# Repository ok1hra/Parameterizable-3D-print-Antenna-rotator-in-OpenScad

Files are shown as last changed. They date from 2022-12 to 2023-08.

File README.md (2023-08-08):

# Parameterizable 3D print Antenna rotator in OpenScad
- Four predefined sizes (S,MS,M,XL)
- Included terminal for install motor from cordless drill
- Without nuts (tapered holes)
- DXF export lasered steel cover
- BOM included
- With Azimuth potentiometer (MS,M,XL)
- With Homing endstop, for using with stepper motor (MS,M,XL)

## Assembly manual
- [RemoteQTH Wiki](https://remoteqth.com/w/doku.php?id=3d-print-rotator)
- [GitHub copy](Assembly-manual.md)

## Related components
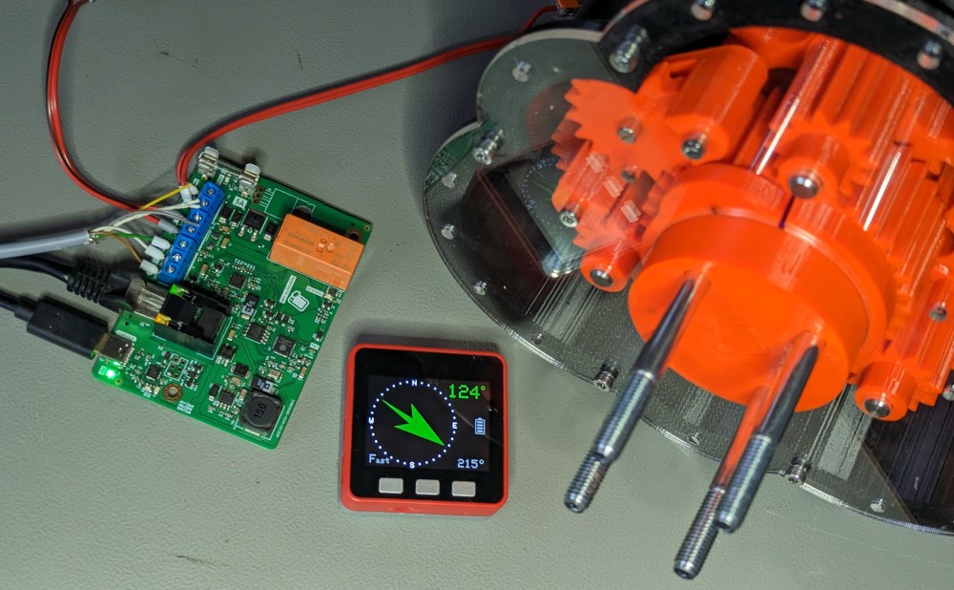
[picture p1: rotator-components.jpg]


- [IP-rotator firmware](https://github.com/ok1hra/IP-rotator)
- IP-rotator hardware - TBD
- [Gyrotator](https://github.com/ok1hra/gyrotator)

## Output files
- Source [OpenScad file](parametric-3d-rotator.scad) for design customisation
- Render bash script [.sh](render-stl.sh) need modify local path

### S size
(compromise design without endstop and azimuth potentiometer)
- [BOM](S.echo)
- Steel cover [.DXF](S.DXF)
- Steel output terminal [.DXF](Sout.DXF)
- All [.STL](/S)
- [S_in.3mf](S_in.3mf)
- [S_out.3mf](S_out.3mf)

### M size (recommended)
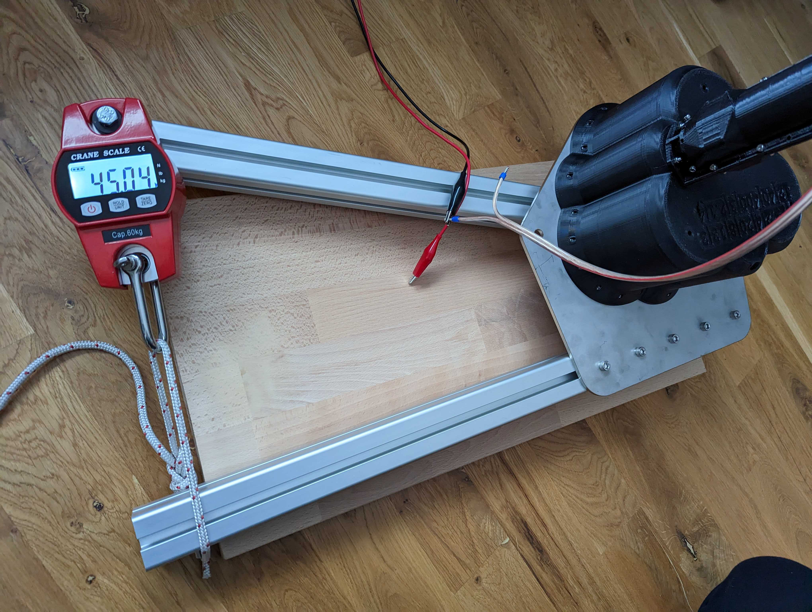
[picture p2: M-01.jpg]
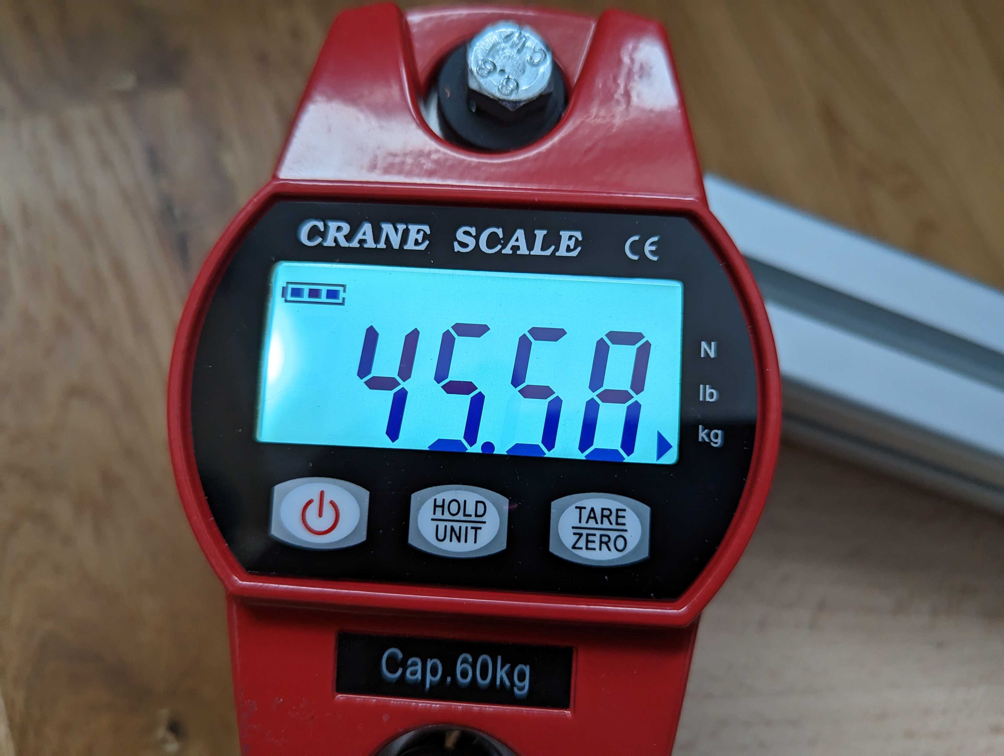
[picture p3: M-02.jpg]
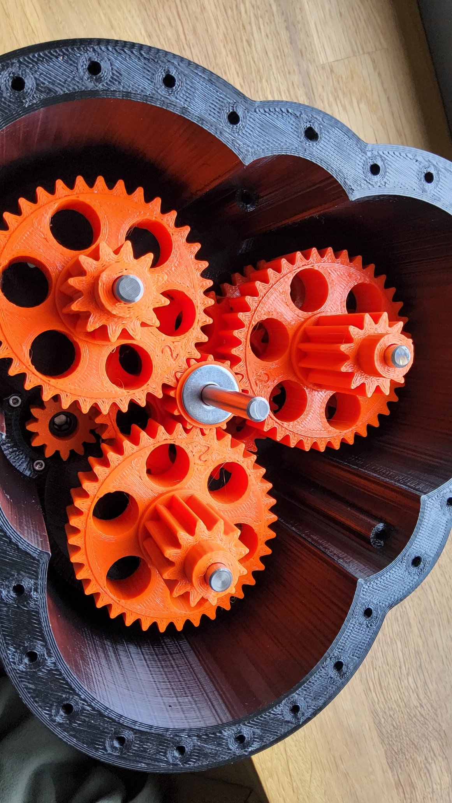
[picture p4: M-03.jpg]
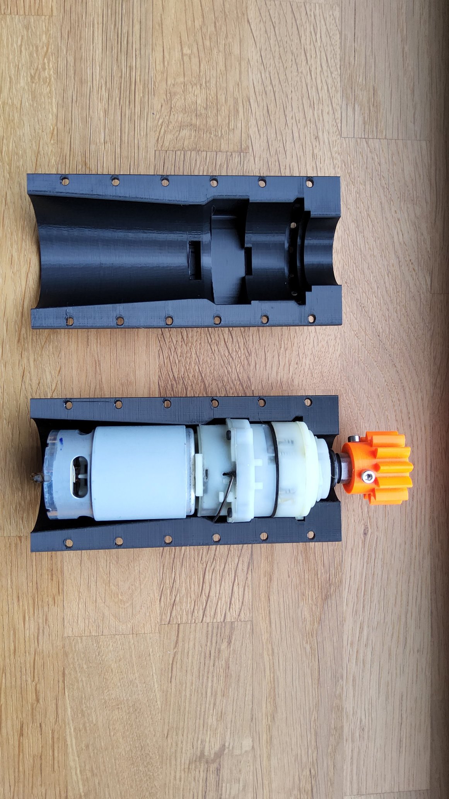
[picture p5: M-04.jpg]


- Max torque **2200 kg/cm (215 N/m)**
- [Torque video](https://www.youtube.com/watch?v=XpkWt55Bdf4)
- [BOM](M.echo)
- Steel cover [.DXF](M.DXF)
- Steel output terminal [.DXF](Mout.DXF)
- All [.STL](/M)
- [M_in.3mf](M_in.3mf)
- [M_out.3mf](M_out.3mf)

### MS size (smaller version for Prusa MK3 MK4 printers)
- [BOM](MS.echo)
- Steel cover [.DXF](MS.DXF)
- Steel output terminal [.DXF](MSout.DXF)
- All [.STL](/MS)
- [M_in.3mf](MS_in.3mf)

### XL size
- [BOM](XL.echo)
- Steel cover [.DXF](XL.DXF)
- Steel output terminal [.DXF](XLout.DXF)
- All [.STL](/XL)
- [XL_in.3mf](XL_in.3mf)
- [XL_out1.3mf](XL_out1.3mf)
- [XL_out2.3mf](XL_out2.3mf)

* [Homepage](https://remoteqth.com/3d-rotator.php)

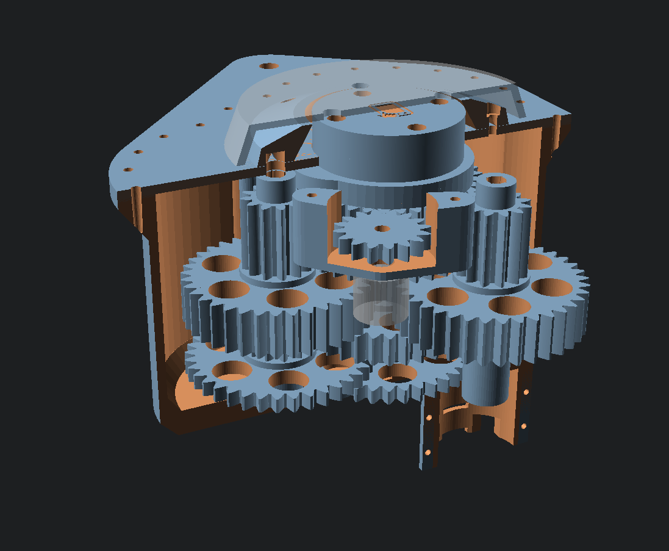
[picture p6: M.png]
preview

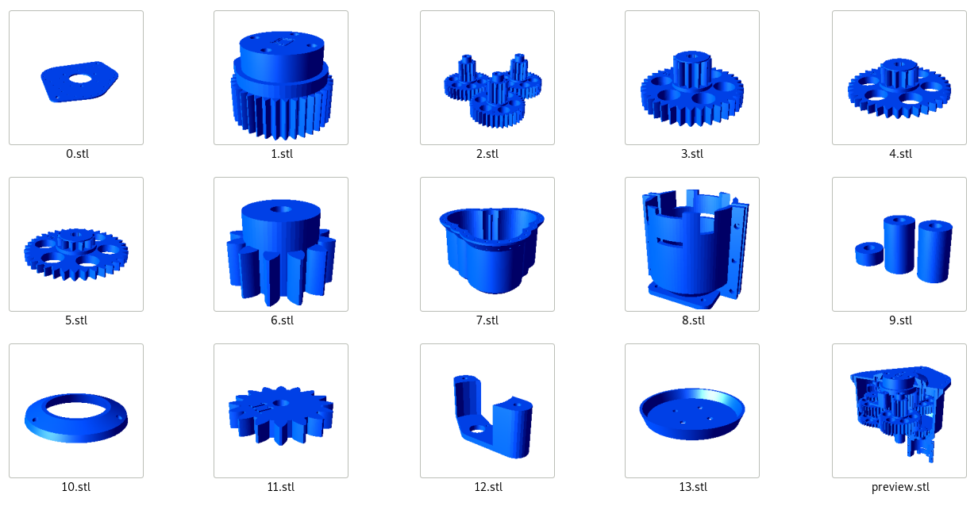
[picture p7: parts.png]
parts


* [OpenScad](https://openscad.org/)

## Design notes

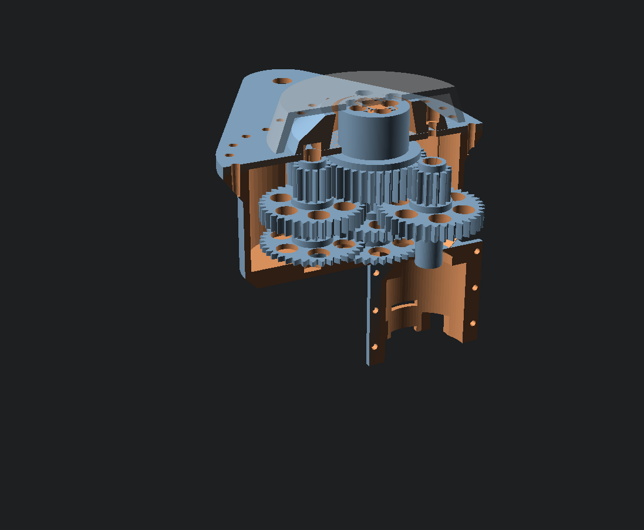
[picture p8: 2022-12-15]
S.png

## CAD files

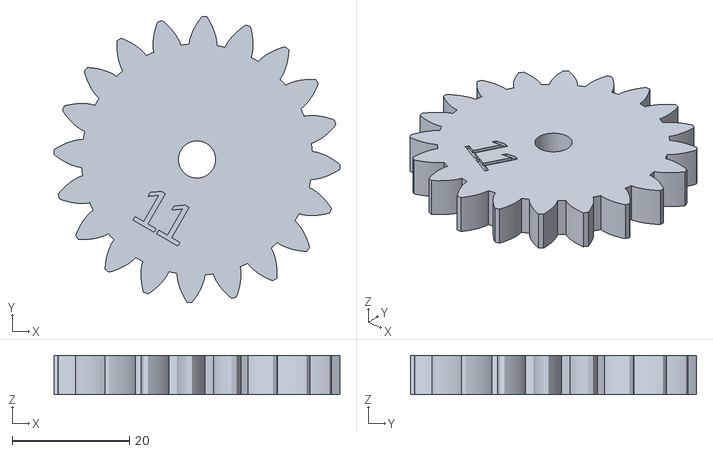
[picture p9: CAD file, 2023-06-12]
M/11.stl
48.9 x 48.9 x 6.67

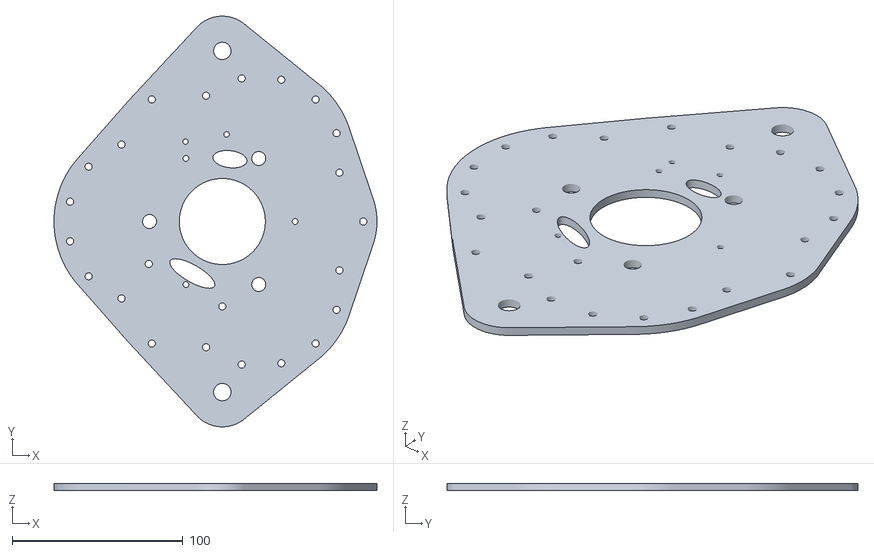
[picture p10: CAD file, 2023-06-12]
MS/0.stl
189.3 x 240.8 x 4.00

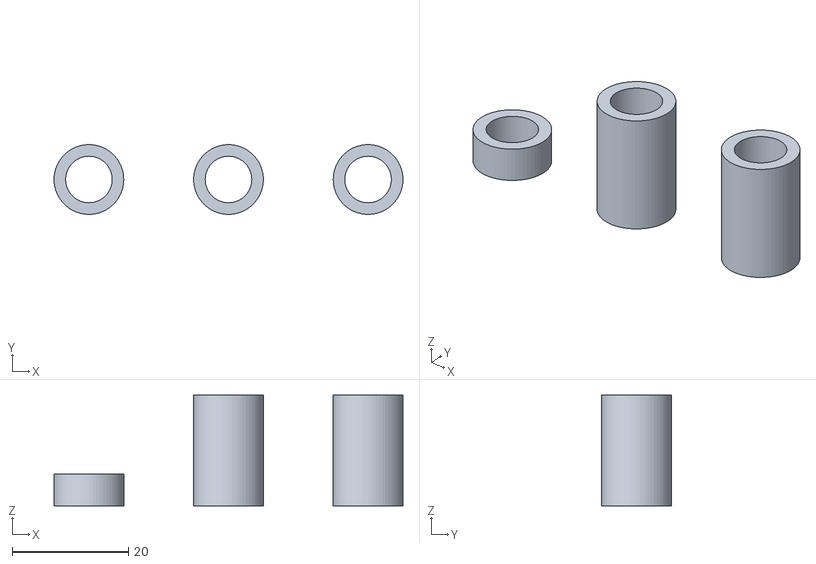
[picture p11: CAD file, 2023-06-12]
S/9.stl
60.0 x 12.0 x 19.0

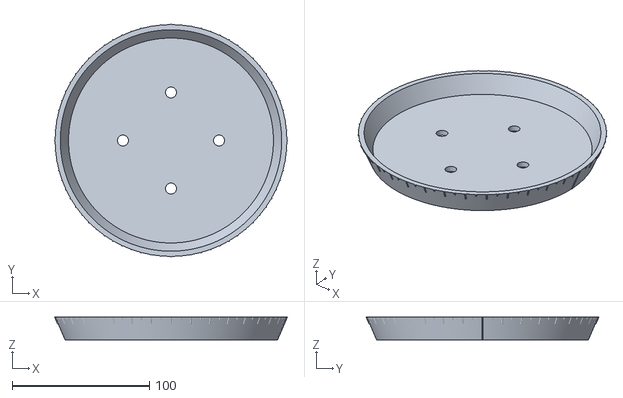
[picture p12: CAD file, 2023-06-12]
XL/13.stl
169.8 x 169.8 x 16.8

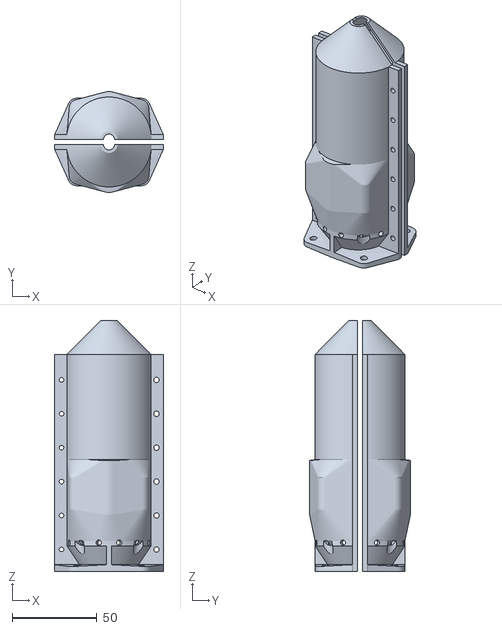
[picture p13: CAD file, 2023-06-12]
M/8.stl
64.0 x 59.5 x 148.0

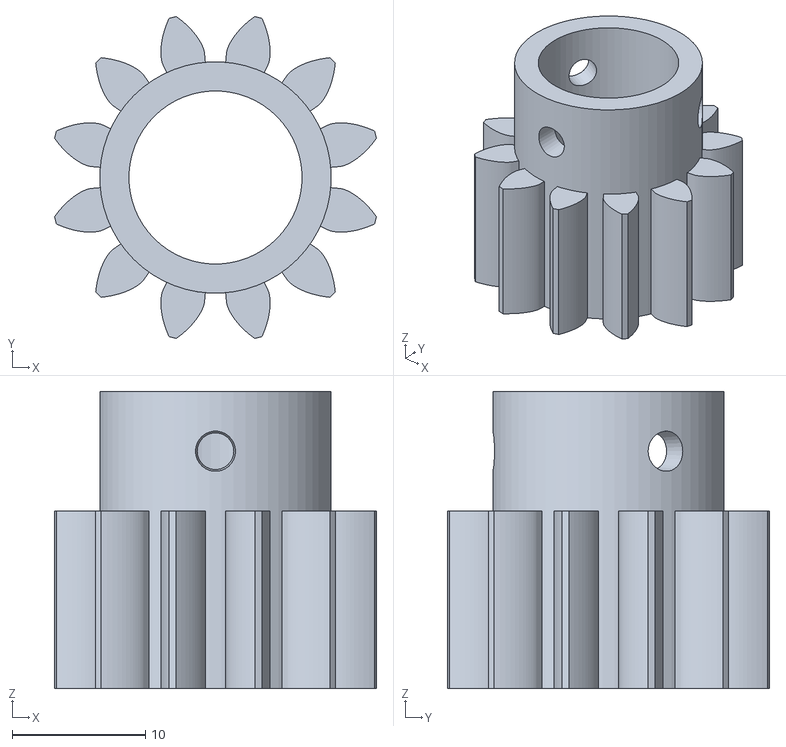
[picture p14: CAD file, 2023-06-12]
MS/6.stl
24.2 x 24.2 x 22.3

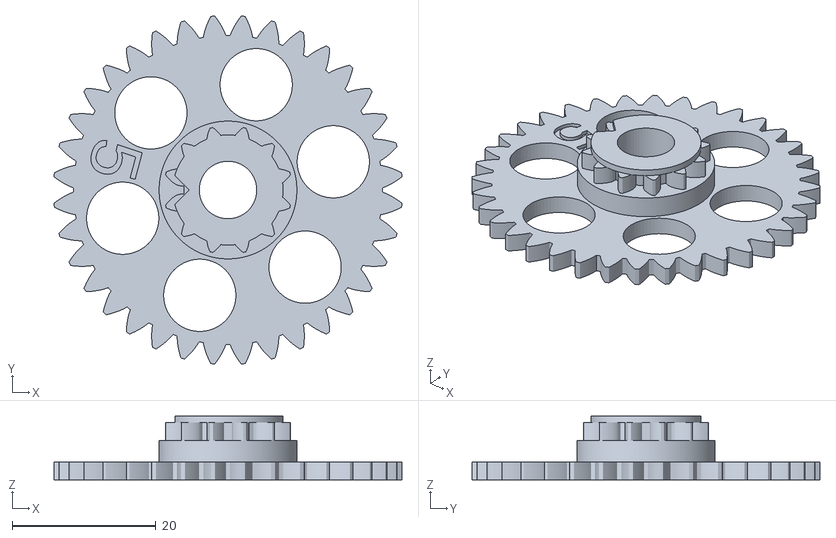
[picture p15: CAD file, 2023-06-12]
S/5.stl
48.4 x 48.4 x 8.90

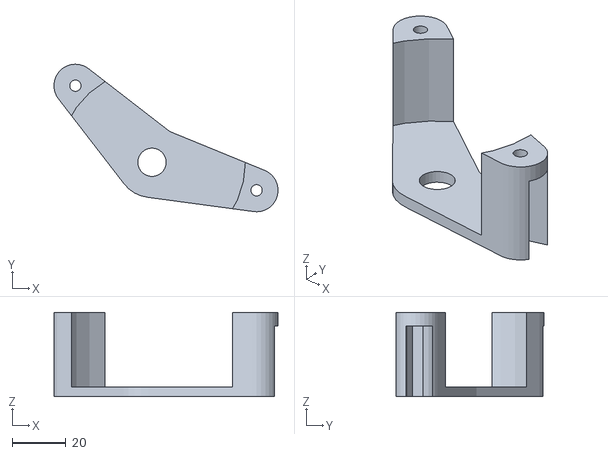
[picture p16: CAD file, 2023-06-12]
XL/12.stl
83.3 x 54.9 x 31.3

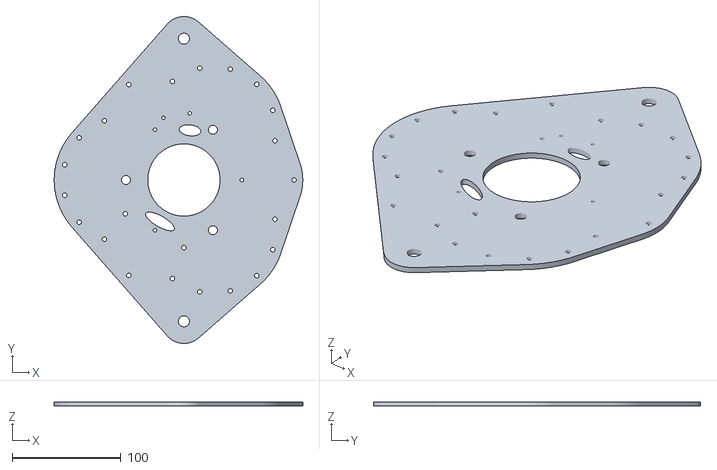
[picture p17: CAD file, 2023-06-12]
M/0.stl
228.7 x 300.8 x 4.00

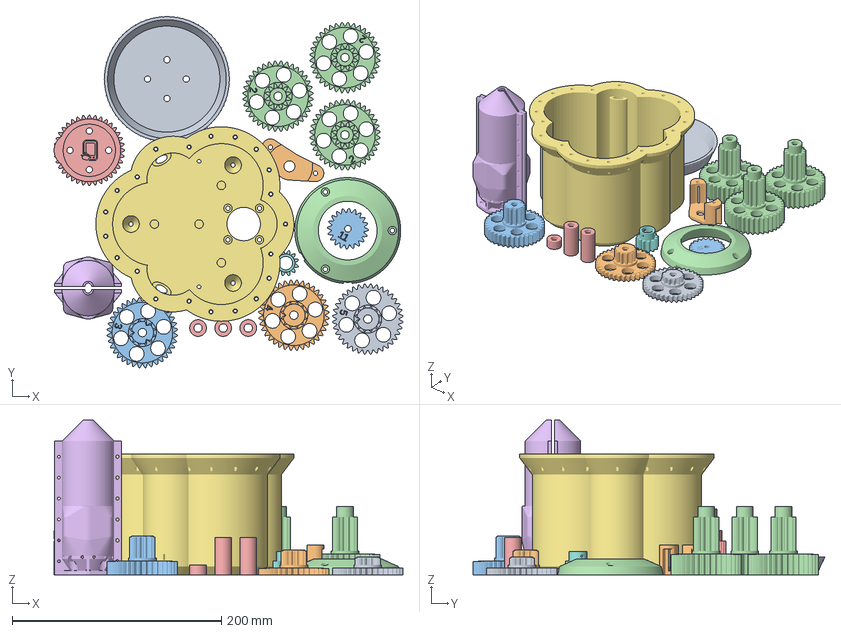
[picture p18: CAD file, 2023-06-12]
MS-xl.3mf
333.7 x 336.3 x 148.0 mm
13.stl
12.stl
11.stl
10.stl
9.stl
8.stl
7.stl
6.stl
5.stl
4.stl
3.stl
2.stl
1.stl

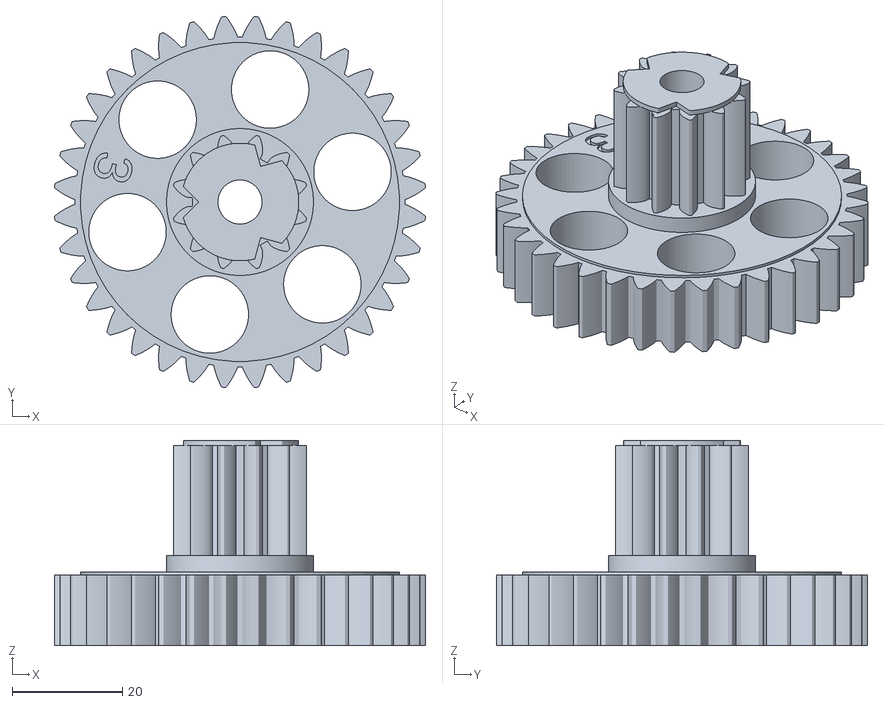
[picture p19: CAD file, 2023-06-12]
MS/3.stl
67.4 x 67.4 x 37.2

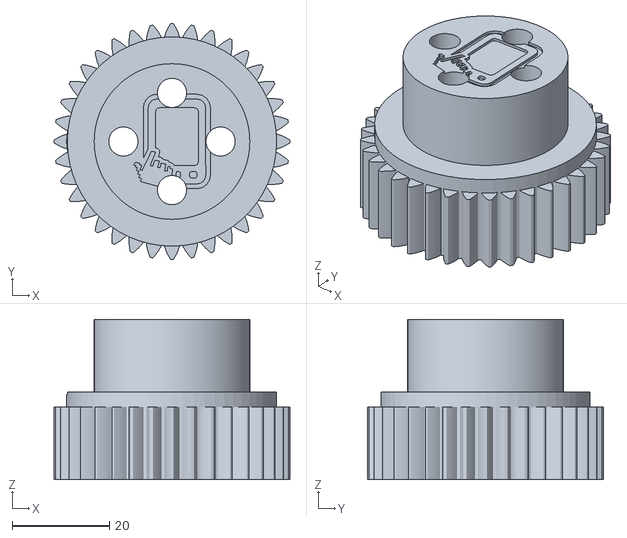
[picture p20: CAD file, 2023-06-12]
S/1.stl
48.6 x 48.6 x 33.0

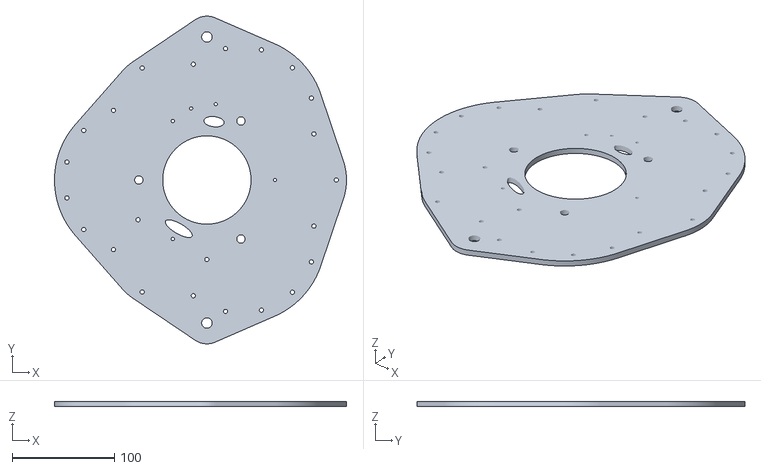
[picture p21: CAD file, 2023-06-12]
XL/0.stl
285.8 x 320.8 x 5.00

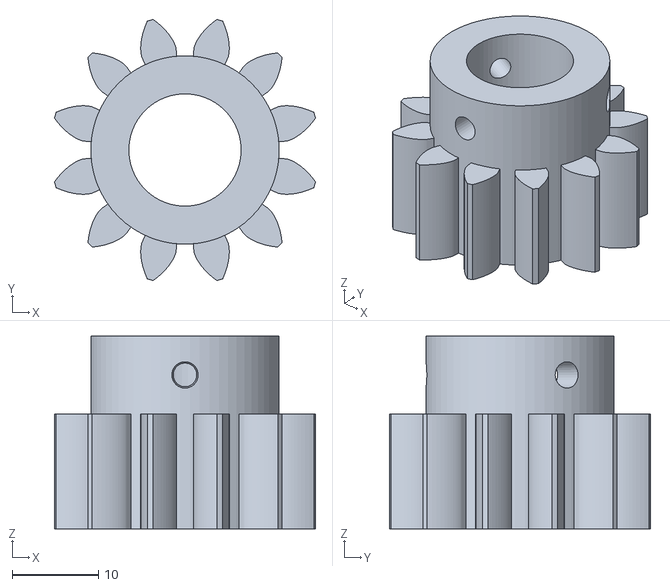
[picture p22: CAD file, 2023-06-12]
M/6.stl
30.2 x 30.2 x 22.3

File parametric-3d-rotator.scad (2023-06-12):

/*
 Parametric 3D print antenna rotator
 © 2010 by OK1HRA https://remoteqth.com/3d-rotator.php
 Creative Commons BY-SA
 -------------------------------------------------------------------
 Gear module
 Parametric Involute Bevel and Spur Gears by GregFrost
 It is licensed under the Creative Commons - GNU LGPL 2.1 license.
 © 2010 by GregFrost, thingiverse.com/Amp
 http://www.thingiverse.com/thing:3575 and http://www.thingiverse.com/thing:3752
-------------------------------------------------------------------
 How to export .stl
 After open change inputs parameters and press F5
 .STL export press F6 and menu /Design/Export as STL...

 How to export .dxf
 - set PartNumber to 0 or 13
 - set DXFexport to 1
 - render [F6]
 - menu File/Export/ExportDXF
----------------- Input parameter ---------------------------------*/

    RotatorMountingPointsDiameter   =  10.2     ;// it must be sufficiently robust
    AntMountScrewRadius             =   0       ;// 0 for auto, if greater than zero, the value is used (18.5 first version dimension)
    FlangeScrewDiameter             =   4       ;// 4 optimal size
    ScrewHoleTolerance              =   0.2     ;// it creates clearance and compensates for the inaccuracy of the 3d printer
    InAxisDiameter                  =   8.0     ;// main internal axes
    MotorMountType                  =   2       ;// [1-2] part #8 | type 1 from unknown parkside | motor type 2 from PARKSIDE PBSA 12 D4 (max 28 Nm, 350/1 300 RPM)
    MotorMountZshift                =   8       ;// in mm, expand part #8 in Z
    MotorAxisDiameter               =  13       ;// according to the selected motor - part #6
    MotorShaftFlattening            =   0       ;// in mm, if need - part #6
    MotorShaftScrew                 =   3       ;// in mm, if need - part #6, 0 for disable
    SmallNumberOfTeeth              =  12       ;// smaller gear
    VerticalSpacing                 =   3       ;// between gears
    PlainBearingHeight              =   2.1     ;// smaller than VerticalSpacing
    PotentiometerAxisDiameter       =   6.34    ;// according to the selected potentiometer
    PotentiometerMountAxisDiameter  =  10.5     ;// according to the selected potentiometer
    PotentiometerExpand             =   6+2       ;// number of  teeth
    BodyPrimaryExpander             =   1.25    ;// bigger than 1.2
    BodySecondExpander              =   1.4     ;// bigger than 1.2
    IndentedDiameter                =   7       ;// part #1
    EndstopRotate                   = 165       ;// do not change
    CircularPitchLimitUnderWhichDisableEndstopAndPotetniometer = 390   ;// I recommend not to change, because not space in small design
    TorqueMountingPoints            = 0        ;// [0] only for measure
    DXFexport                       =   0       ;// [0-1] off/on for part #0 and #13
    PartNumber                      =    -13       ;// export parts [0-13], preview all [negative value]
    
// ----------------- Small size---------------------------------
    
//    AntMountScrewDiameter           =   6       ;// it must be sufficiently robust  (>6)
//    AntMountScrewHead               =  10.2     ;// measure the screw used (M8 13.2, M6 10.2)
//    AntWheelHeight                  =  15       ;// bigger than 15
//    RotatorMountingPointsPitch      = 200       ;// check that it exceeds the dimension of part number seven
//    TransferRatio                   =   3       ;// full transfer ratio for 3 = 243 | for 4 = 1024
//    FirstHeight                     =  15       ;// gear height number one is used to calculate the height of the others gear
//    CircularPitch                   = 230       ;
//    BoxThickness                    =   3       ;// wall thickness of part number seven

// ----------------- Small, but usable---------------------------------

//    AntMountScrewDiameter           =   8       ;// it must be sufficiently robust  (>6)
//    AntMountScrewHead               =  13.2     ;// measure the screw used (M8 13.2, M6 10.2)
//    AntWheelHeight                  =  20       ;// bigger than 15
//    RotatorMountingPointsPitch      = 260       ;// check that it exceeds the dimension of part number seven
//    TransferRatio                   =   3       ;// full transfer ratio for 3 = 243 | for 4 = 1024
//    FirstHeight                     =  40-10       ;// gear height number one is used to calculate the height of the others gear
//    CircularPitch                   = 400       ;
//    BoxThickness                    =   4       ;// wall thickness of part number seven

// ----------------- Medium size---------------------------------

    AntMountScrewDiameter           =   8       ;// it must be sufficiently robust  (>6)
    AntMountScrewHead               =  13.2     ;// measure the screw used (M8 13.2, M6 10.2)
    AntWheelHeight                  =  20       ;// bigger than 15
    RotatorMountingPointsPitch      = 260       ;// check that it exceeds the dimension of part number seven
    TransferRatio                   =   3       ;// full transfer ratio for 3 = 243 | for 4 = 1024
    FirstHeight                     =  40       ;// gear height number one is used to calculate the height of the others gear
    CircularPitch                   = 400       ;
    BoxThickness                    =   4       ;// wall thickness of part number seven

// ----------------- Big size---------------------------------

//    AntMountScrewDiameter           =   8       ;// it must be sufficiently robust  (>6)
//    AntMountScrewHead               =  13.2     ;// measure the screw used (M8 13.2, M6 10.2)
//    AntWheelHeight                  =  20       ;// bigger than 15
//    RotatorMountingPointsPitch      = 280       ;// check that it exceeds the dimension of part number seven
//    TransferRatio                   =   3       ;// full transfer ratio for 3 = 243 | for 4 = 1024
//    FirstHeight                     =  50       ;// gear height number one is used to calculate the height of the others gear
//    CircularPitch                   = 500       ;
//    BoxThickness                    =   5       ;// wall thickness of part number seven

//================================================

//    ToDo
//    - box for control electronics
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

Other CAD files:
M.DXF
MSout.DXF
MS/9.stl
S/3.stl
M/1.stl
M/10.stl
M/12.stl
M/13.stl
M/3.stl
M/4.stl
M/5.stl
M/9.stl
MS-in.3mf
MS.DXF
MS/1.stl
MS/10.stl
MS/11.stl
MS/12.stl
MS/13.stl
MS/4.stl
MS/5.stl
MS/8.stl
M_in.3mf
M_out.3mf
Mout.DXF
S.DXF
S/0.stl
S/10.stl
S/13.stl
S/4.stl
S/6.stl
S_in.3mf
S_out.3mf
Sout.DXF
V_166_1A006.stl
XL.DXF
XL/1.stl
XL/10.stl
XL/11.stl
XL/3.stl
XL/4.stl
XL/5.stl
XL/6.stl
XL/8.stl
XL/9.stl
XL_in.3mf
XL_out1.3mf
XL_out2.3mf
XLout.DXF

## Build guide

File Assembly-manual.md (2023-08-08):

# 3D print rotator (revision 2023)

[Source files on GitHub](https://github.com/ok1hra/Parameterizable-3D-print-Antenna-rotator-in-OpenScad#m-size-recommended)  
I include the source file in OpenScad and several preset exports, in dimensions S, M, MS, XL. Size M is recommended, MS reduced for Prusa MK3 and MK4 printers. I also include the following data for each dimension:

-   BOM
-   Steel cover .DXF
-   .STL files
-   .3mf preset

Printed parts  
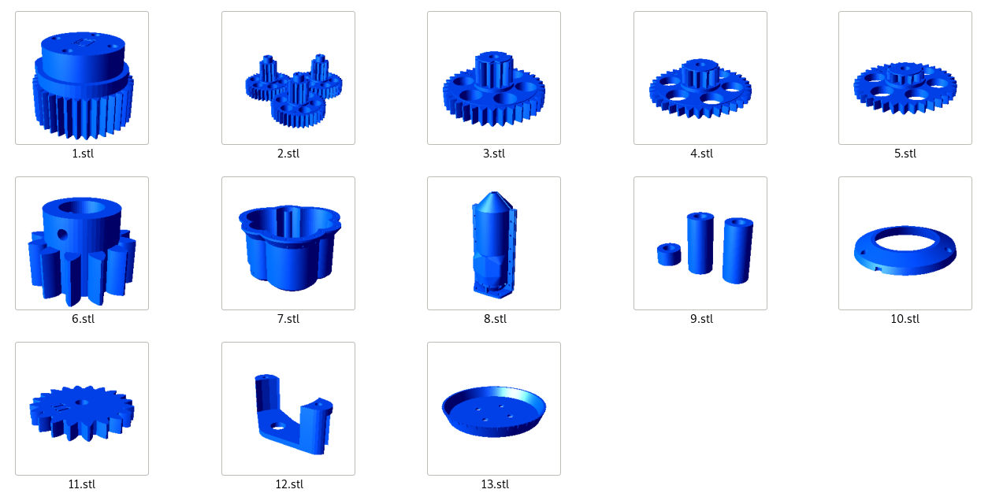
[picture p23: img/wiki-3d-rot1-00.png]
  

## BOM

<table>
<tbody>
<tr class="odd">
<td>https://raw.githubusercontent.com/ok1hra/Parameterizable-3D-print-Antenna-rotator-in-OpenScad/main/img/wiki-3d-rot1-00.png</td>
<td>Printed parts<br />
Prefered black PETG filament</td>
<td>13 pieces</td>
</tr>
<tr class="even">
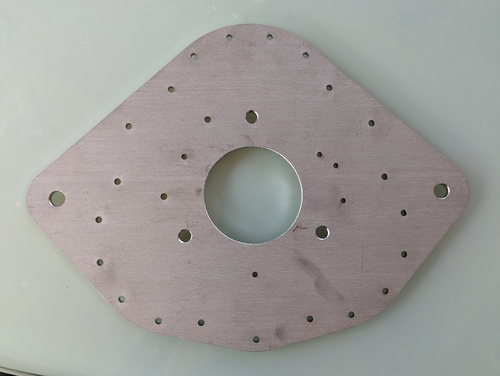
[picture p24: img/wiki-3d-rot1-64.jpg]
https://raw.githubusercontent.com/ok1hra/Parameterizable-3D-print-Antenna-rotator-in-OpenScad/main/img/wiki-3d-rot1-64.jpg
<td></td>
<td>Top cover 4mm thick from stainless steel<br />
By .DXF file from <a href="https://github.com/ok1hra/Parameterizable-3D-print-Antenna-rotator-in-OpenScad#m-size-recommended">GitHub</a> depending on the size</td>
<td>1 piece</td>
</tr>
<tr class="odd">
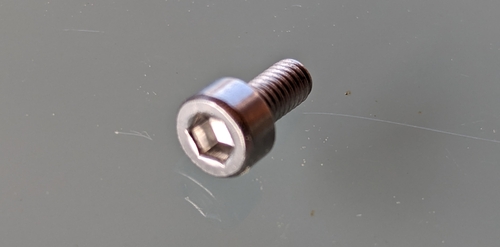
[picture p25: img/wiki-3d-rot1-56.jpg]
https://raw.githubusercontent.com/ok1hra/Parameterizable-3D-print-Antenna-rotator-in-OpenScad/main/img/wiki-3d-rot1-56.jpg
<td></td>
<td>M3 x 6mm, allen head, stainless steel</td>
<td>3 pieces</td>
</tr>
<tr class="even">
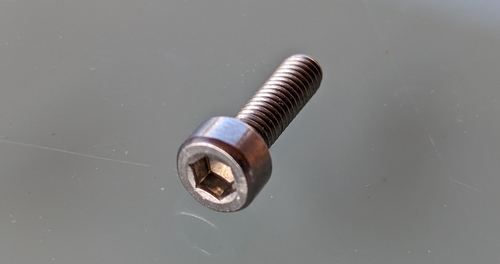
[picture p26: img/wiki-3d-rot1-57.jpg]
https://raw.githubusercontent.com/ok1hra/Parameterizable-3D-print-Antenna-rotator-in-OpenScad/main/img/wiki-3d-rot1-57.jpg
<td></td>
<td>M3 x 10mm, allen head, stainless steel</td>
<td>11 pieces</td>
</tr>
<tr class="odd">
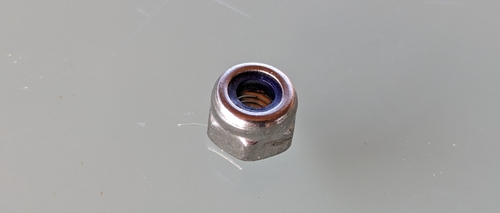
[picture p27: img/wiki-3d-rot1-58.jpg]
https://raw.githubusercontent.com/ok1hra/Parameterizable-3D-print-Antenna-rotator-in-OpenScad/main/img/wiki-3d-rot1-58.jpg
<td></td>
<td>M3 nuts, stainless steel</td>
<td>8 pieces</td>
</tr>
<tr class="even">
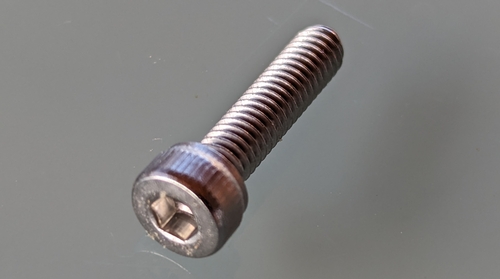
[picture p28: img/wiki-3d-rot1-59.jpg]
https://raw.githubusercontent.com/ok1hra/Parameterizable-3D-print-Antenna-rotator-in-OpenScad/main/img/wiki-3d-rot1-59.jpg
<td></td>
<td>M4 x 16 mm, allen head, stainless steel</td>
<td>32 pieces</td>
</tr>
<tr class="odd">
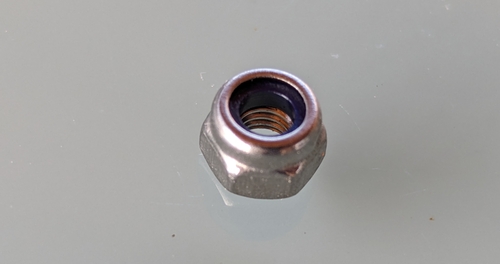
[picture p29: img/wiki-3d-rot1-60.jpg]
https://raw.githubusercontent.com/ok1hra/Parameterizable-3D-print-Antenna-rotator-in-OpenScad/main/img/wiki-3d-rot1-60.jpg
<td></td>
<td>M4 nuts, stainless steel</td>
<td>6 pieces</td>
</tr>
<tr class="even">
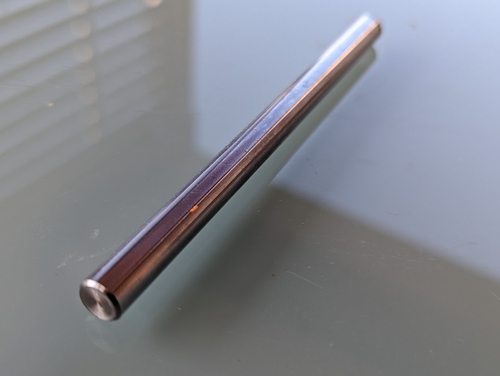
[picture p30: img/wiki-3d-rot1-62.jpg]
https://raw.githubusercontent.com/ok1hra/Parameterizable-3D-print-Antenna-rotator-in-OpenScad/main/img/wiki-3d-rot1-62.jpg
<td></td>
<td>Smoothed axis 8mm (length according to size, see bom on <a href="https://github.com/ok1hra/Parameterizable-3D-print-Antenna-rotator-in-OpenScad#m-size-recommended">GitHub</a>)</td>
<td>4 pieces</td>
</tr>
<tr class="odd">
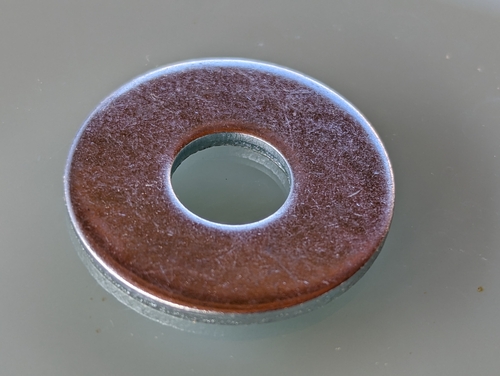
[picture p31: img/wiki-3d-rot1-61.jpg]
https://raw.githubusercontent.com/ok1hra/Parameterizable-3D-print-Antenna-rotator-in-OpenScad/main/img/wiki-3d-rot1-61.jpg
<td></td>
<td>1.9mm thick (critical size!) metal washer, Inner diameter 8.5 mm, Outer diameter 23 mm</td>
<td>7 pieces</td>
</tr>
<tr class="even">
<td></td>
<td>M8 x 100 mm</td>
<td>4 pieces</td>
</tr>
<tr class="odd">
<td></td>
<td>M8 nuts</td>
<td>4 pieces</td>
</tr>
<tr class="even">
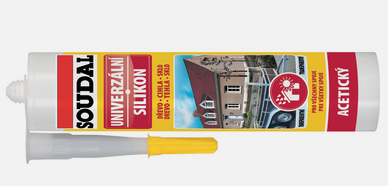
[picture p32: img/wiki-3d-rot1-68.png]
https://raw.githubusercontent.com/ok1hra/Parameterizable-3D-print-Antenna-rotator-in-OpenScad/main/img/wiki-3d-rot1-68.png
<td></td>
<td>Universal transparent silicone sealant</td>
<td>100g</td>
</tr>
<tr class="odd">
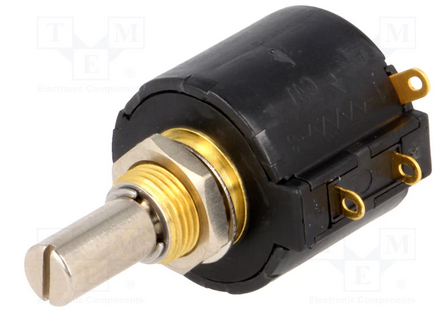
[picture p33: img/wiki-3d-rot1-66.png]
https://raw.githubusercontent.com/ok1hra/Parameterizable-3D-print-Antenna-rotator-in-OpenScad/main/img/wiki-3d-rot1-66.png
<td></td>
<td><a href="https://www.tme.eu/cz/details/3547s-1aa-102a/potenciometry-viceotackove-dratove/bourns/">Azimuth potentiometer Bourns 3547S-1AA-102A</a></td>
<td>1 piece</td>
</tr>
<tr class="even">
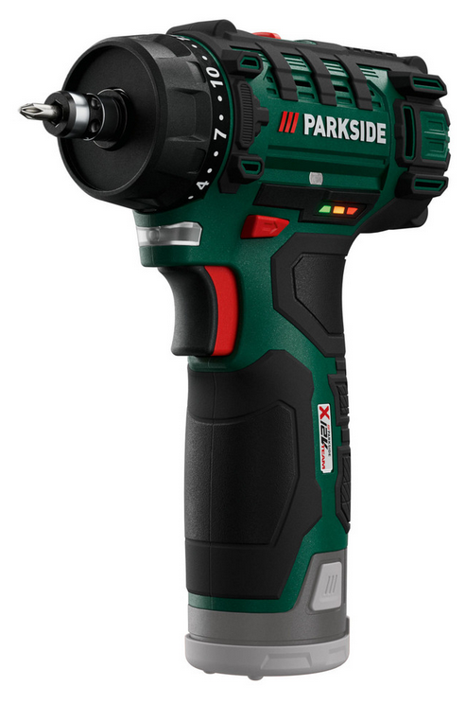
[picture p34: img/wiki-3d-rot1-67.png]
https://raw.githubusercontent.com/ok1hra/Parameterizable-3D-print-Antenna-rotator-in-OpenScad/main/img/wiki-3d-rot1-67.png
<td></td>
<td>Motor from PARKSIDE PBSA 12 D4 drill</td>
<td>1 piece</td>
</tr>
<tr class="odd">
<td></td>
<td>2x 1.5mm wires, 20 cm long</td>
<td>1 piece</td>
</tr>
<tr class="even">
<td></td>
<td>3x 1.5mm wires, 40 cm long</td>
<td>1 piece</td>
</tr>
<tr class="odd">
<td>https://raw.githubusercontent.com/ok1hra/Parameterizable-3D-print-Antenna-rotator-in-OpenScad/main/img/wiki-3d-rot1-76.png</td>
<td>crimping ends for guides</td>
<td>5 pieces</td>
</tr>
<tr class="even">
<td></td>
<td>Universal lubricant</td>
<td>200g</td>
</tr>
<tr class="odd">
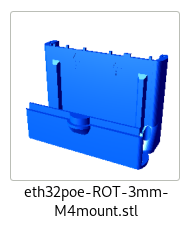
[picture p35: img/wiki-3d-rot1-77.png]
https://raw.githubusercontent.com/ok1hra/Parameterizable-3D-print-Antenna-rotator-in-OpenScad/main/img/wiki-3d-rot1-77.png
<td></td>
<td>3D print box for Simple Rotator Interface V. electronics (optional)<br />
Mounted in step 16</td>
<td>1 pieces</td>
</tr>
</tbody>
</table>

## Tools

| | |
|---|---|
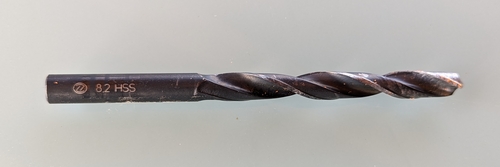
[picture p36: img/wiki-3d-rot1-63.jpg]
https://raw.githubusercontent.com/ok1hra/Parameterizable-3D-print-Antenna-rotator-in-OpenScad/main/img/wiki-3d-rot1-63.jpg
|  | Drill 8,2mm |
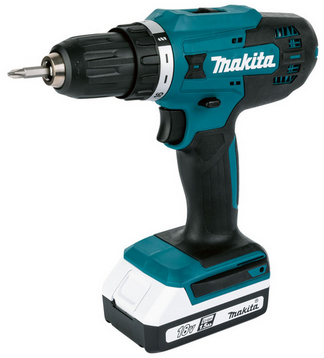
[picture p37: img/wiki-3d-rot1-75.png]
https://raw.githubusercontent.com/ok1hra/Parameterizable-3D-print-Antenna-rotator-in-OpenScad/main/img/wiki-3d-rot1-75.png
|  | Drill machine |
| https://raw.githubusercontent.com/ok1hra/Parameterizable-3D-print-Antenna-rotator-in-OpenScad/main/img/wiki-3d-rot1-69.png | Allen key 2mm |
| https://raw.githubusercontent.com/ok1hra/Parameterizable-3D-print-Antenna-rotator-in-OpenScad/main/img/wiki-3d-rot1-69.png | Allen key 2,5mm |
| https://raw.githubusercontent.com/ok1hra/Parameterizable-3D-print-Antenna-rotator-in-OpenScad/main/img/wiki-3d-rot1-70.png | Key 5,5mm |
| https://raw.githubusercontent.com/ok1hra/Parameterizable-3D-print-Antenna-rotator-in-OpenScad/main/img/wiki-3d-rot1-70.png | Key 7mm |
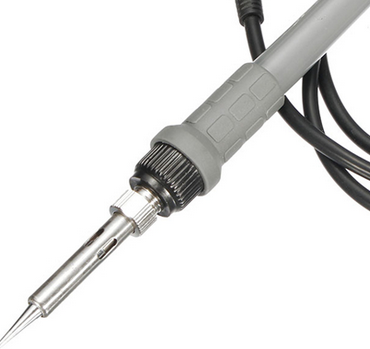
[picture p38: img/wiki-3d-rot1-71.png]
https://raw.githubusercontent.com/ok1hra/Parameterizable-3D-print-Antenna-rotator-in-OpenScad/main/img/wiki-3d-rot1-71.png
|  | Solder station |
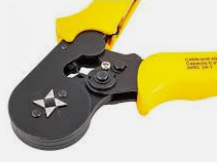
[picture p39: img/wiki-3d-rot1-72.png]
https://raw.githubusercontent.com/ok1hra/Parameterizable-3D-print-Antenna-rotator-in-OpenScad/main/img/wiki-3d-rot1-72.png
|  | Crimping tool |
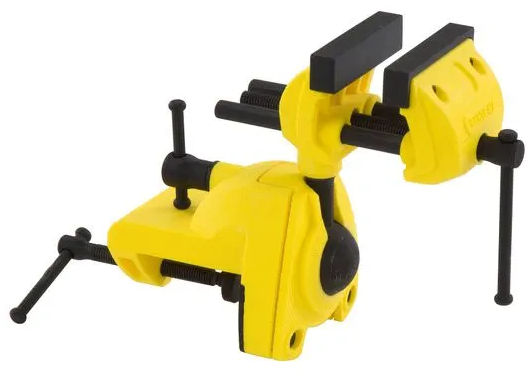
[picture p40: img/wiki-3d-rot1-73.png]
https://raw.githubusercontent.com/ok1hra/Parameterizable-3D-print-Antenna-rotator-in-OpenScad/main/img/wiki-3d-rot1-73.png
|  | Vise |
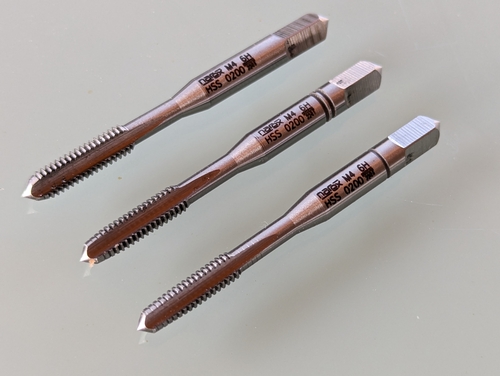
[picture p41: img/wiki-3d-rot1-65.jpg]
https://raw.githubusercontent.com/ok1hra/Parameterizable-3D-print-Antenna-rotator-in-OpenScad/main/img/wiki-3d-rot1-65.jpg
|  | Set for cutting threads M4 |
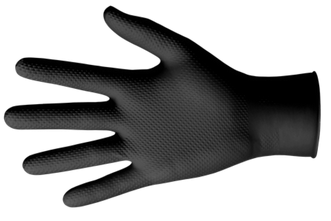
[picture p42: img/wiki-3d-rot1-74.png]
https://raw.githubusercontent.com/ok1hra/Parameterizable-3D-print-Antenna-rotator-in-OpenScad/main/img/wiki-3d-rot1-74.png
|  | Protective gloves for applying lubricant |

------------------------------------------------------------------------

# Assembly manual, step by step

1.  Before disassembly drill tool for extract motor, set the gear ratio
    to 1 (slow), and the torque to maximum (drill)
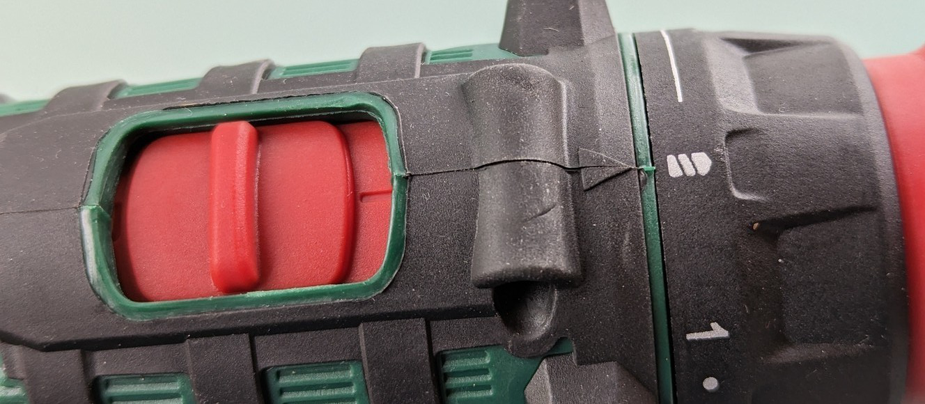
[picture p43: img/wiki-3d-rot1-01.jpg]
https://raw.githubusercontent.com/ok1hra/Parameterizable-3D-print-Antenna-rotator-in-OpenScad/main/img/wiki-3d-rot1-01.jpg
      
1.  Remove the two U-shaped springs from the battery space  
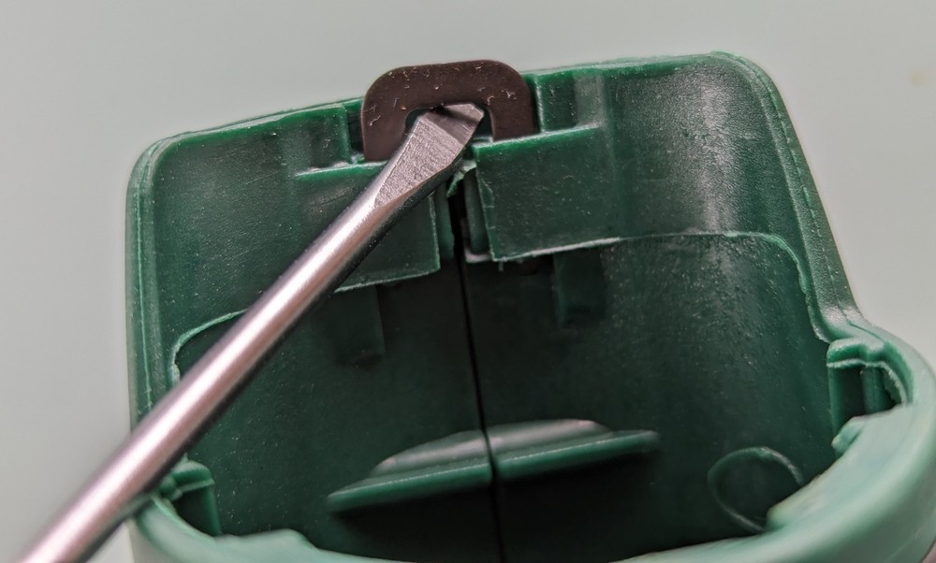
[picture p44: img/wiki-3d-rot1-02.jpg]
https://raw.githubusercontent.com/ok1hra/Parameterizable-3D-print-Antenna-rotator-in-OpenScad/main/img/wiki-3d-rot1-02.jpg
    
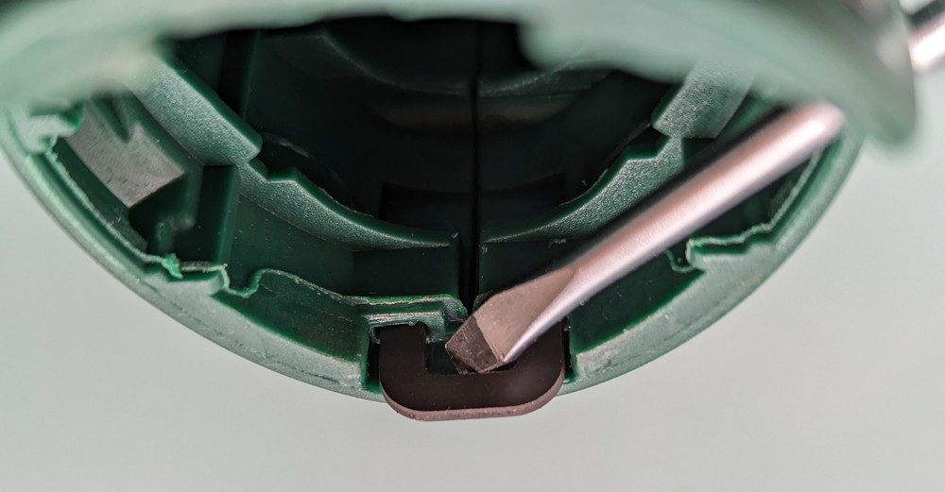
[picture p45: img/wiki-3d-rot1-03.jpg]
https://raw.githubusercontent.com/ok1hra/Parameterizable-3D-print-Antenna-rotator-in-OpenScad/main/img/wiki-3d-rot1-03.jpg
      
1.  Unscrew the seven screws, remove the chuck and open cover
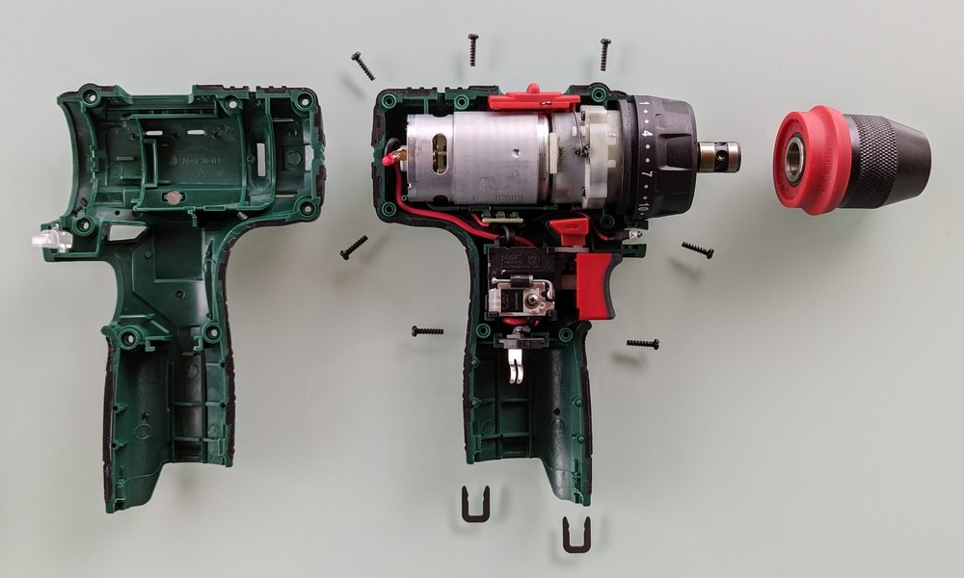
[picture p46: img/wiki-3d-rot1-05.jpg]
      
1.  Sign polarity on the motor (+ on red wire)  
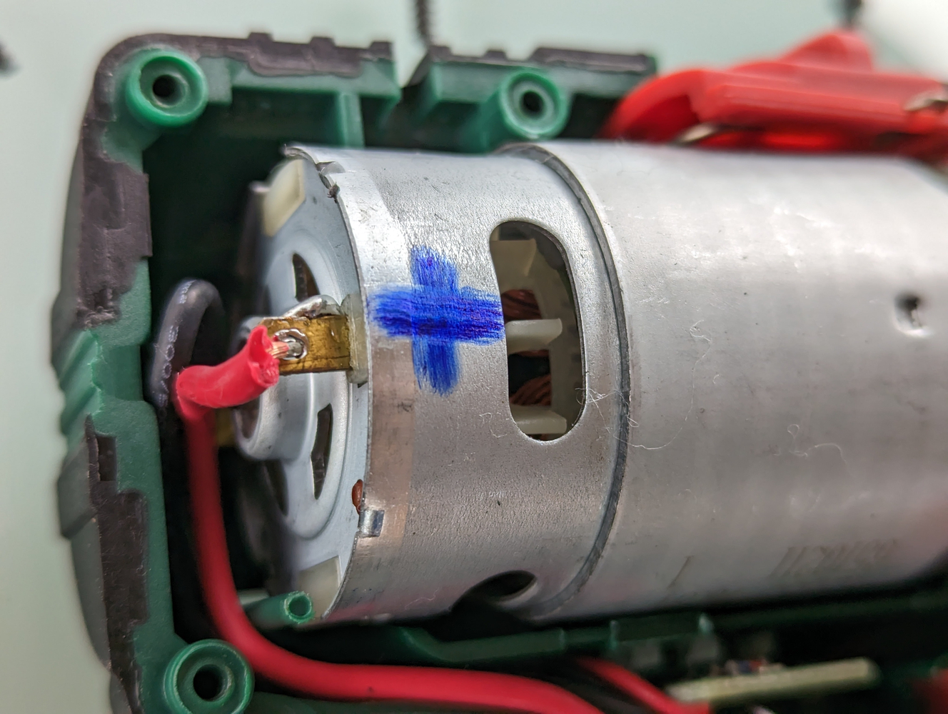
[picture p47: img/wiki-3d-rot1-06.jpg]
https://raw.githubusercontent.com/ok1hra/Parameterizable-3D-print-Antenna-rotator-in-OpenScad/main/img/wiki-3d-rot1-06.jpg
      
1.  Solder 20 cm of power cable with crimped ends

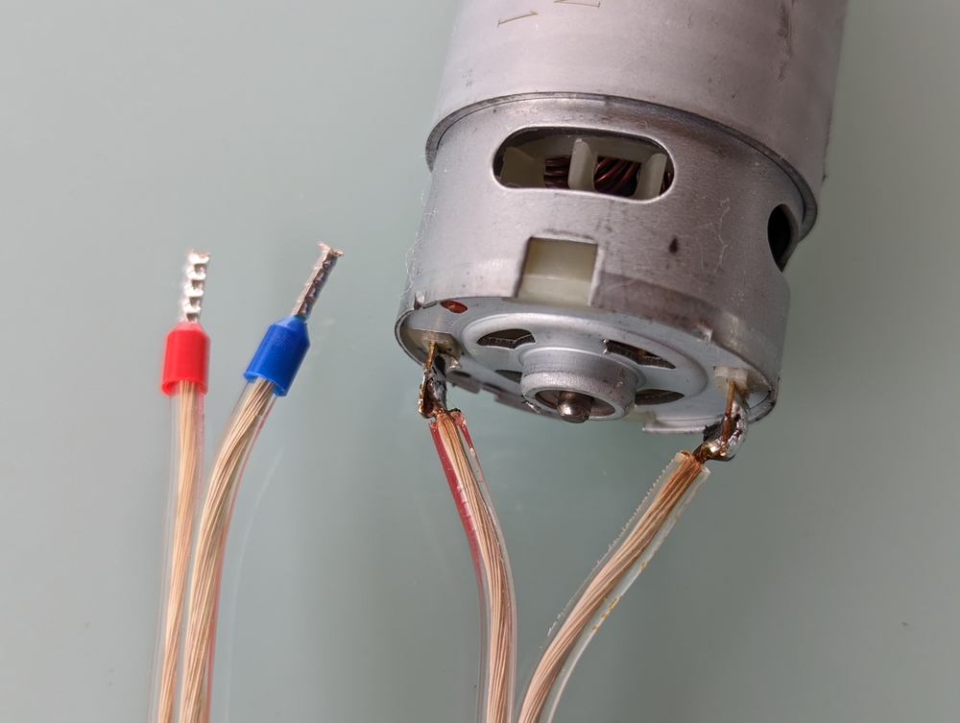
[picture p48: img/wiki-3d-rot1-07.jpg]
https://raw.githubusercontent.com/ok1hra/Parameterizable-3D-print-Antenna-rotator-in-OpenScad/main/img/wiki-3d-rot1-07.jpg
      
1.  The wago terminal block is suitable for general use, for the
    connection of the Simple Rotator Interface V. use the prescribed
    connector  
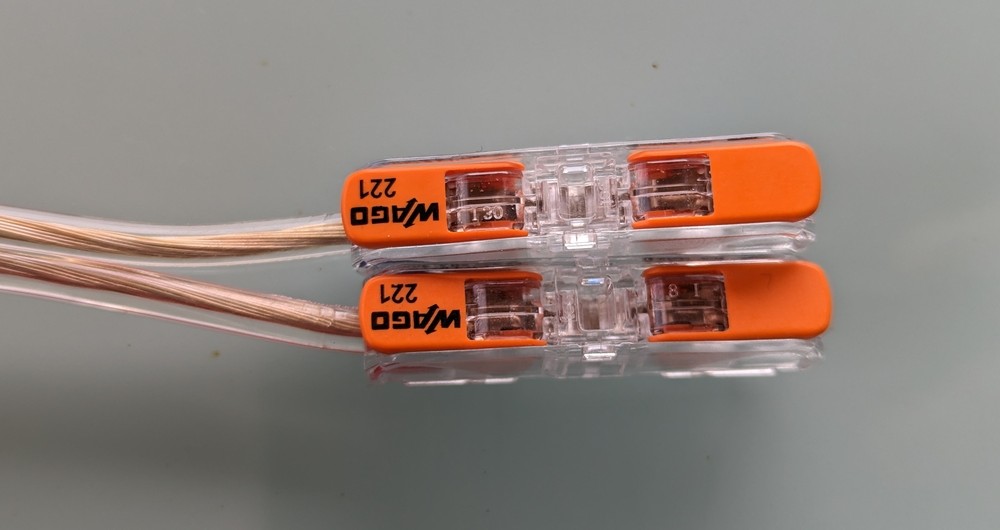
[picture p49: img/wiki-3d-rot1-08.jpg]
https://raw.githubusercontent.com/ok1hra/Parameterizable-3D-print-Antenna-rotator-in-OpenScad/main/img/wiki-3d-rot1-08.jpg
    
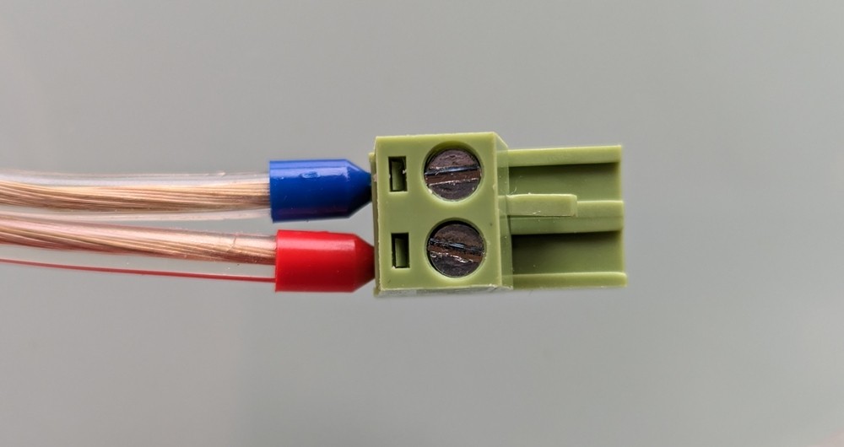
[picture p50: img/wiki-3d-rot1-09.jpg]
https://raw.githubusercontent.com/ok1hra/Parameterizable-3D-print-Antenna-rotator-in-OpenScad/main/img/wiki-3d-rot1-09.jpg
      
1.  Make sure the gear ratio stick is set to the slow position  
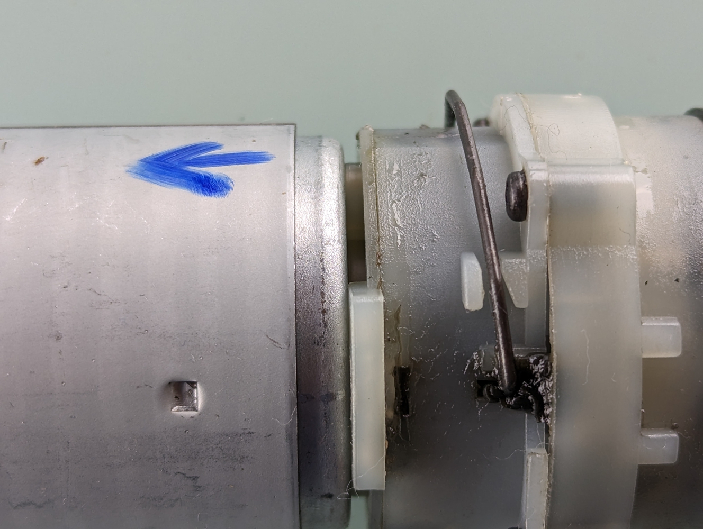
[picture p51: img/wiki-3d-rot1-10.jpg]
https://raw.githubusercontent.com/ok1hra/Parameterizable-3D-print-Antenna-rotator-in-OpenScad/main/img/wiki-3d-rot1-10.jpg
      
1.  Insert the motor into the half of the printed plastic housing
    8.stl  
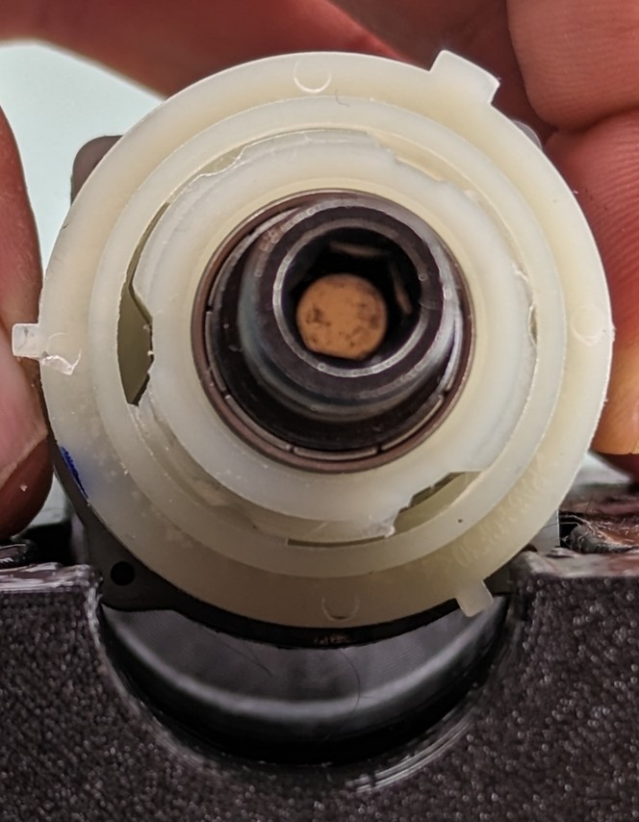
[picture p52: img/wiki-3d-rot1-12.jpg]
https://raw.githubusercontent.com/ok1hra/Parameterizable-3D-print-Antenna-rotator-in-OpenScad/main/img/wiki-3d-rot1-12.jpg
      
1.  The orientation of the motor can be seen in the photo. The plastic
    wheel in the middle is facing up.
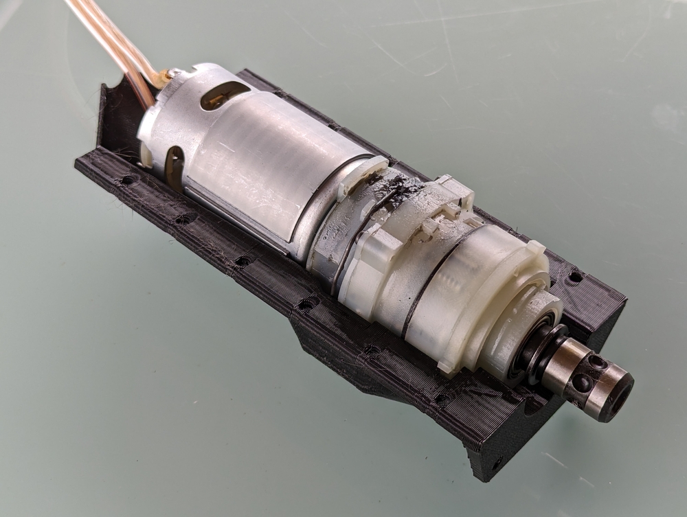
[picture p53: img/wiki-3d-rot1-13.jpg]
      
1.  Again make sure the gear ratio stick is set to the slow position  
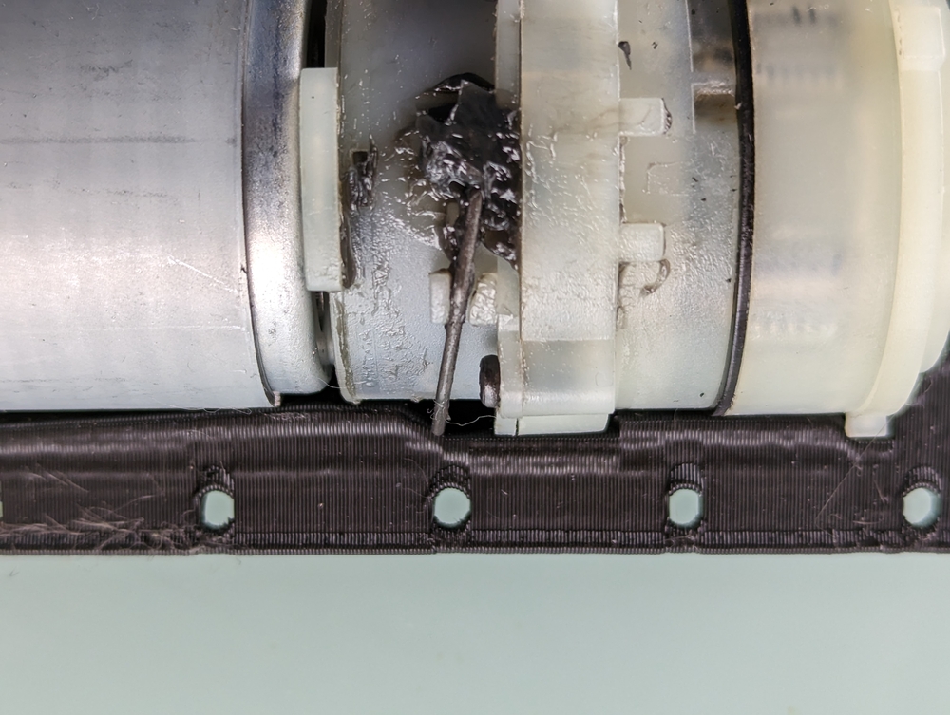
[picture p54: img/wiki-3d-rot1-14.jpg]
https://raw.githubusercontent.com/ok1hra/Parameterizable-3D-print-Antenna-rotator-in-OpenScad/main/img/wiki-3d-rot1-14.jpg
      
1.  Apply silicone sealant around the entire perimeter of the plastic
    holder  
    Fix the gearbox spring in the slow position with silicone
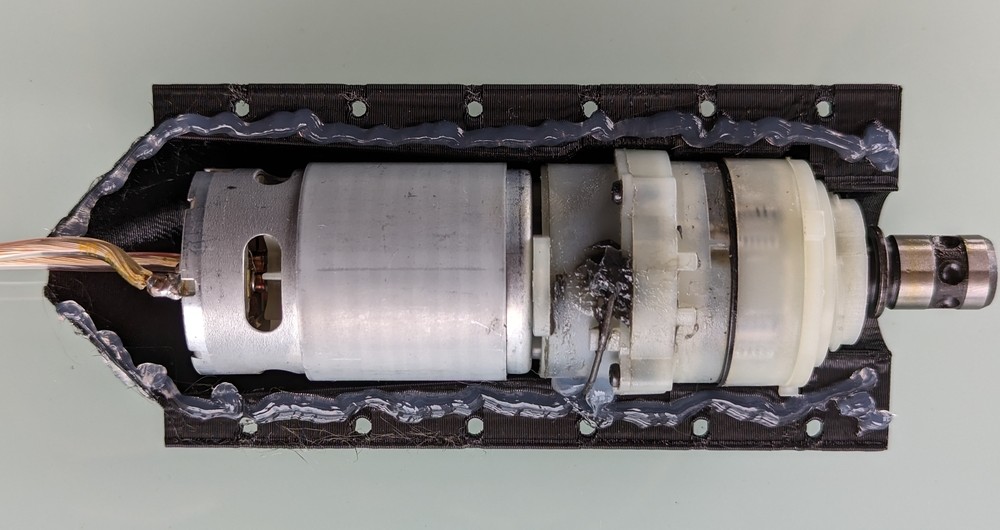
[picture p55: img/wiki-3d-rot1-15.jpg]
      
1.  Close the motor using the second pulley of the plastic motor
    holder, and secure with a minimum of four M3x10 screws with a lock
    nut on each side
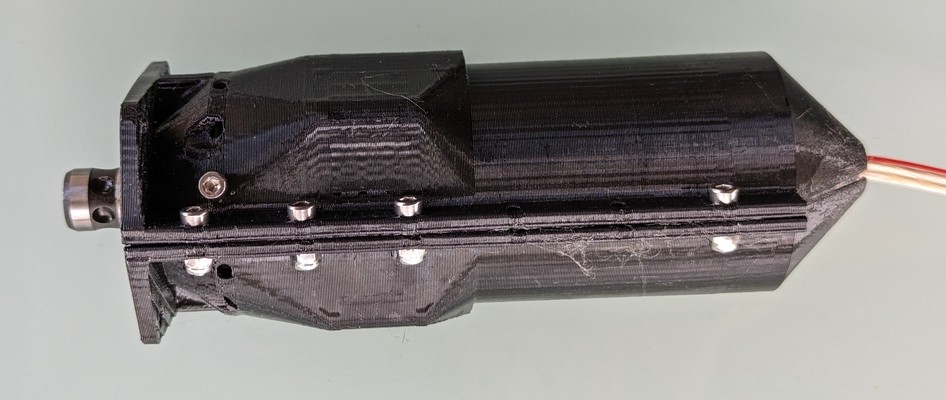
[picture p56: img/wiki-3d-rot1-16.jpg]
      
1.  Install three M3x6 screws around the perimeter so that they do not
    collide with the three protrusions from step 8. Tighten very
    sensitively, the screws do not have metal nuts, but screw directly
    into the plastic.  
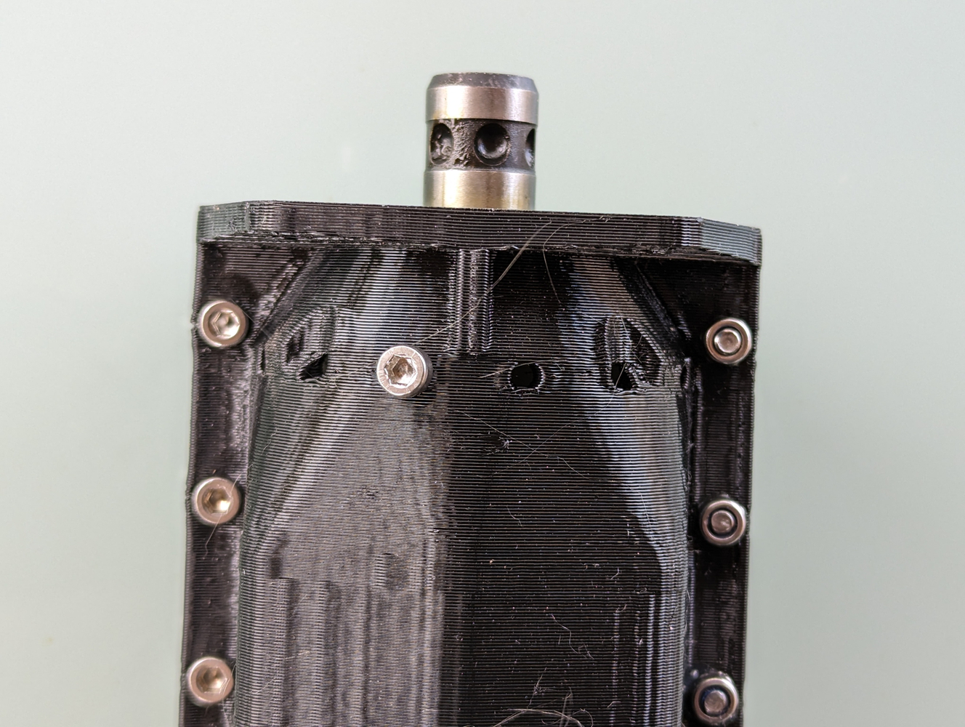
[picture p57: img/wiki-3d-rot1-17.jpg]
https://raw.githubusercontent.com/ok1hra/Parameterizable-3D-print-Antenna-rotator-in-OpenScad/main/img/wiki-3d-rot1-17.jpg
      
1.  Press the 6.stl gear onto the motor shaft so that the side holes
    are directly against the depressions in the motor shaft. Then screw
    three M3x10 screws into the hole - screw in sensitively and stop as
    soon as the resistance increases - it is screwed directly into the
    plastic. We recommend applying secondary glue to the plastic hole
    before inserting the screw.  
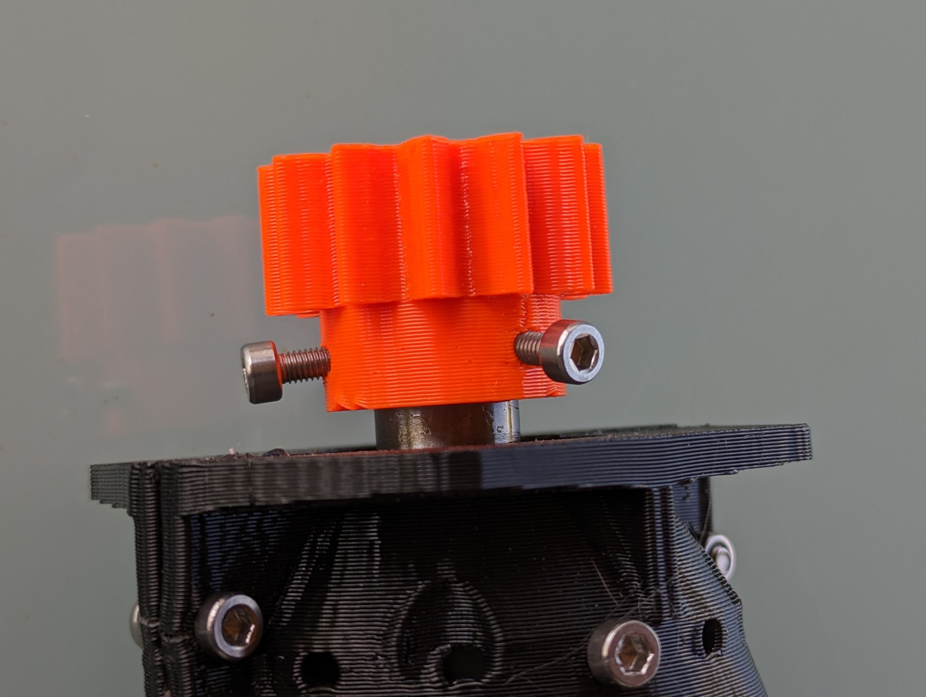
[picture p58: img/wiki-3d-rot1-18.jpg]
https://raw.githubusercontent.com/ok1hra/Parameterizable-3D-print-Antenna-rotator-in-OpenScad/main/img/wiki-3d-rot1-18.jpg
      
1.  Attach the entire motor body to the rotator 7.stl main tank using
    four M4x16 screws with lock nuts
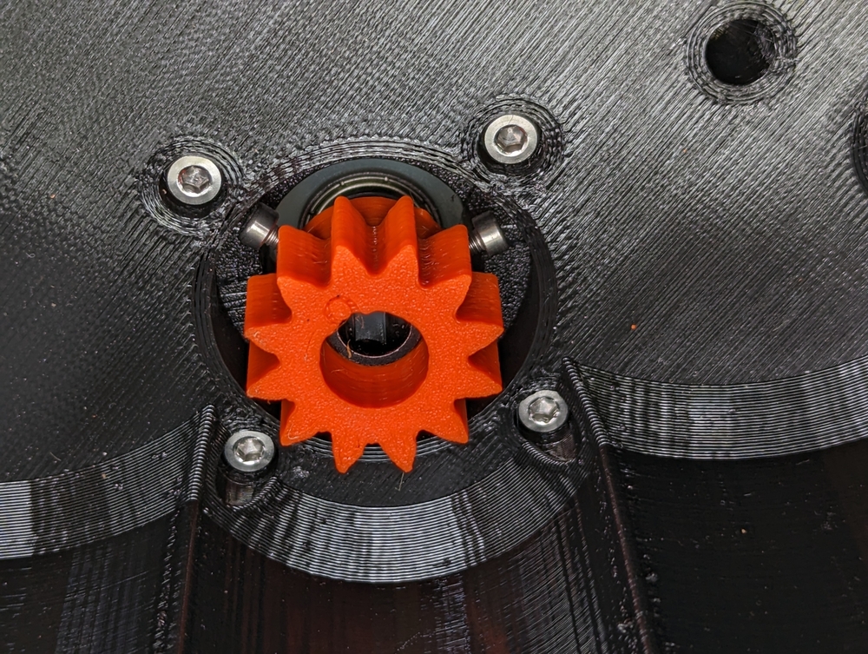
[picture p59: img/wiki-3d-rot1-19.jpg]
https://raw.githubusercontent.com/ok1hra/Parameterizable-3D-print-Antenna-rotator-in-OpenScad/main/img/wiki-3d-rot1-19.jpg
    
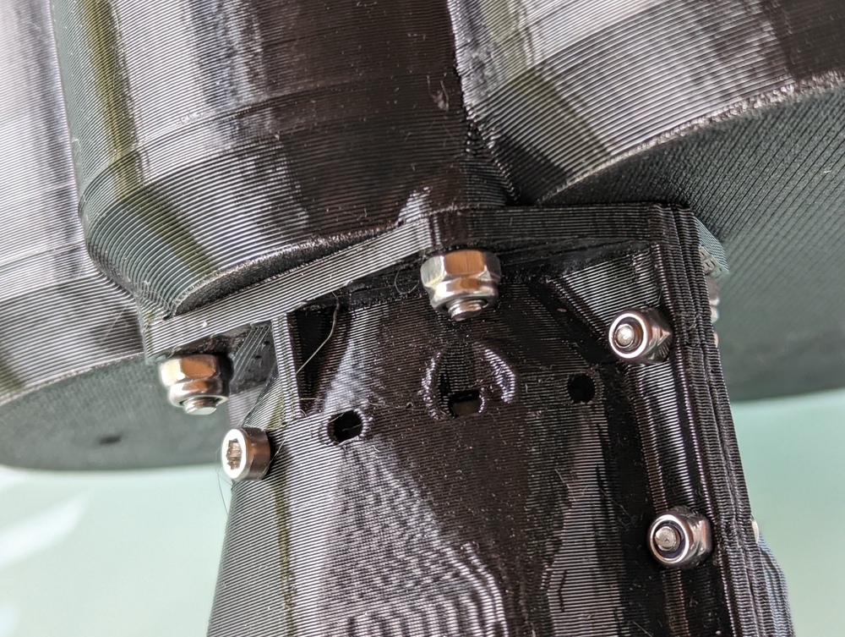
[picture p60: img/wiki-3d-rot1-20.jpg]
https://raw.githubusercontent.com/ok1hra/Parameterizable-3D-print-Antenna-rotator-in-OpenScad/main/img/wiki-3d-rot1-20.jpg
      
1.  If you will use the Simple Rotator Interface V. to control the
    rotator, screw its printed box with two M4x16 screws directly to the
    plastic body of the rotator  
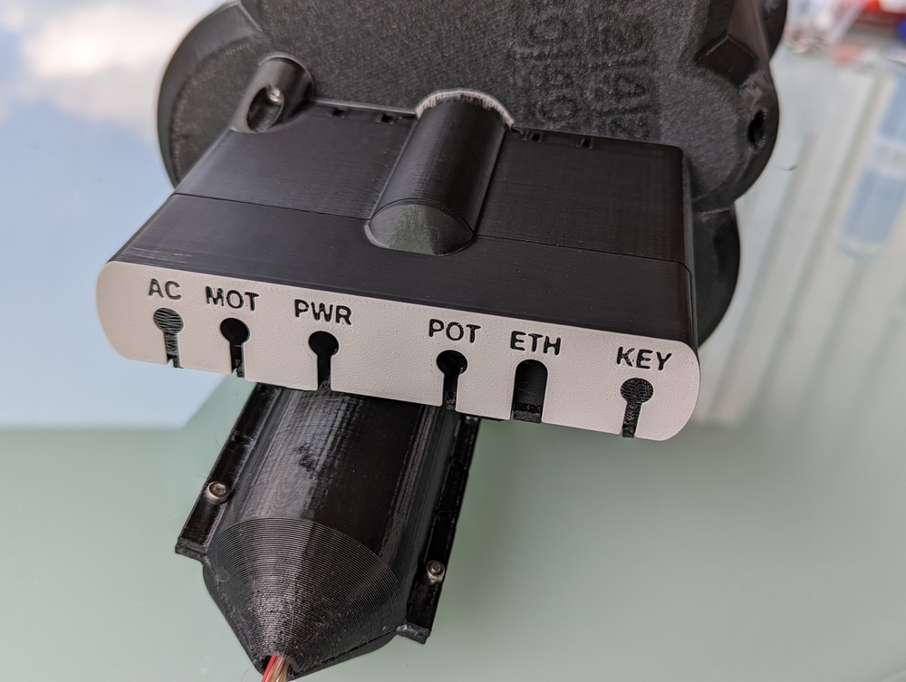
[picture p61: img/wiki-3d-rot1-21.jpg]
https://raw.githubusercontent.com/ok1hra/Parameterizable-3D-print-Antenna-rotator-in-OpenScad/main/img/wiki-3d-rot1-21.jpg
      
1.  In the next step, drill out the axes of the plastic parts number
    1, 2, 3, 4, 5 and 9, with a drill with a diameter of 8.2 mm, so that
    they rotate freely on a smooth axis with a diameter of 8 mm.  
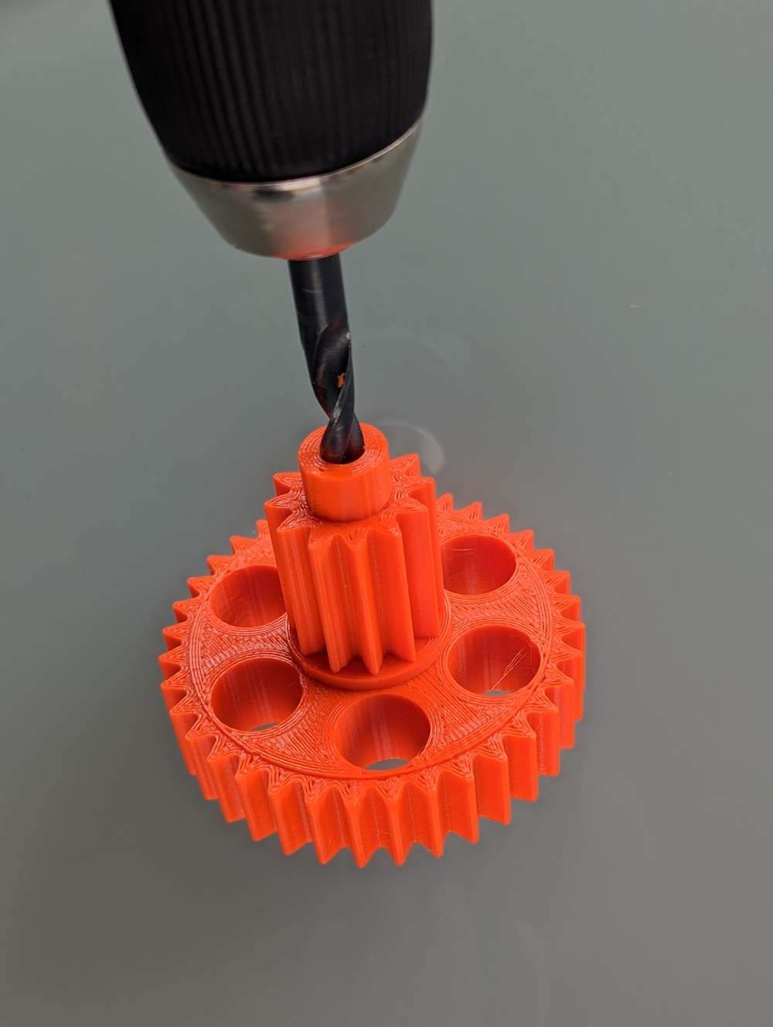
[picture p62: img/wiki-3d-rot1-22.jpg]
https://raw.githubusercontent.com/ok1hra/Parameterizable-3D-print-Antenna-rotator-in-OpenScad/main/img/wiki-3d-rot1-22.jpg
    
    https://raw.githubusercontent.com/ok1hra/Parameterizable-3D-print-Antenna-rotator-in-OpenScad/main/img/wiki-3d-rot1-23.jpg  
1.  Fit the four smoothed axes into the rotator body
    https://raw.githubusercontent.com/ok1hra/Parameterizable-3D-print-Antenna-rotator-in-OpenScad/main/img/wiki-3d-rot1-24.jpg  
1.  You put the metal washer on the central axis, and the low ring
    from the 9.stl on the opposite axis of the motor
      
1.  Now you will fit the gears. Apply universal lubricant to them
    before putting them on
    https://raw.githubusercontent.com/ok1hra/Parameterizable-3D-print-Antenna-rotator-in-OpenScad/main/img/wiki-3d-rot1-26.jpg  
1.  Place gear number five on the central axis, and the metal washer
    on the opposite axis of the motor
    https://raw.githubusercontent.com/ok1hra/Parameterizable-3D-print-Antenna-rotator-in-OpenScad/main/img/wiki-3d-rot1-27.jpg  
1.  The previous picture has the center gear turned backwards. Turn
    the bottom gear so that the V slot on the top faces the next gear
    above it. Then put gear number 4 on the axis opposite to the motor
    so that its V slot is facing the center axis, and slide the metal
    washer onto the center axis.
      
1.  On the two free axes, you put on the higher printed washers of the
    9th stl and on all the outer axes, you put on three metal washers.
    https://raw.githubusercontent.com/ok1hra/Parameterizable-3D-print-Antenna-rotator-in-OpenScad/main/img/wiki-3d-rot1-29.jpg  
1.  Detail of the orientation of the cogwheels, including the
    V-groove  
    https://raw.githubusercontent.com/ok1hra/Parameterizable-3D-print-Antenna-rotator-in-OpenScad/main/img/wiki-3d-rot1-30.jpg  
1.  Before fitting other gears, don't forget to lubricate them with
    universal grease  
    https://raw.githubusercontent.com/ok1hra/Parameterizable-3D-print-Antenna-rotator-in-OpenScad/main/img/wiki-3d-rot1-31.jpg  
1.  Place the 3.stl gear on the center axis so that the V splines
    point to the surrounding axes  
    https://raw.githubusercontent.com/ok1hra/Parameterizable-3D-print-Antenna-rotator-in-OpenScad/main/img/wiki-3d-rot1-32.jpg  
1.  Place the three 2.stl gears on the edge of the axle so that the
    number marking points to the center axle
    https://raw.githubusercontent.com/ok1hra/Parameterizable-3D-print-Antenna-rotator-in-OpenScad/main/img/wiki-3d-rot1-33.jpg  
1.  Detail of mutual position  
    https://raw.githubusercontent.com/ok1hra/Parameterizable-3D-print-Antenna-rotator-in-OpenScad/main/img/wiki-3d-rot1-35.jpg  
1.  Place the metal washer on the center axis
      
1.  Insert four M8 screws into gear 1.stl  
    https://raw.githubusercontent.com/ok1hra/Parameterizable-3D-print-Antenna-rotator-in-OpenScad/main/img/wiki-3d-rot1-38.jpg  
1.  Place the 1.stl gear on the center axis
      
1.  Now screw the three-step potentiometer to part 12.stl, with
    orientation according to the picture.  
    https://raw.githubusercontent.com/ok1hra/Parameterizable-3D-print-Antenna-rotator-in-OpenScad/main/img/wiki-3d-rot1-40.jpg  
1.  Using a vice, very carefully press the 11.STL gear onto the
    potentiometer shaft as shown in the picture
      
1.  Solder three 0.5mm^2 wires, 20cm long, to the potentiometer. Crimp
    the ends with end caps
    https://raw.githubusercontent.com/ok1hra/Parameterizable-3D-print-Antenna-rotator-in-OpenScad/main/img/wiki-3d-rot1-42.jpg  
1.  Cut M4 threads into the three holes of the main stainless steel
    plate as shown in the picture
      
1.  Set the azimuth potentiometer to the center position, and screw it
    to the main stainless plate using two M4x16 screws, plus nuts.  
    https://raw.githubusercontent.com/ok1hra/Parameterizable-3D-print-Antenna-rotator-in-OpenScad/main/img/wiki-3d-rot1-45.jpg
    https://raw.githubusercontent.com/ok1hra/Parameterizable-3D-print-Antenna-rotator-in-OpenScad/main/img/wiki-3d-rot1-46.jpg  
1.  Push the wires through the body of the rotator - pay attention to
    the orientation - they belong to the tunnel located below
      
1.  Place the main stainless steel plate on the rotator body so that
    the outer axes pass through the plate outwards and secure 21 M4x16
    screws. Tighten the screws sensitively, they are cut directly into
    the plastic   
1.  Apply silicone sealant to the perimeter groove of part 10.stl
      
1.  And screw it with three M4x16 screws to the main stainless plate
    https://raw.githubusercontent.com/ok1hra/Parameterizable-3D-print-Antenna-rotator-in-OpenScad/main/img/wiki-3d-rot1-50.jpg  
1.  apply a small amount of silicone sealant to the center wheel and
    then slide part 13.stl onto it
      
1.  Now the rotator is complete, ready for use
      
1.  An example of using a rotator under a mast
      
1.

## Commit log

2022-12-15 add .stl exports
    [0.stl, 1.stl, 10.stl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]
2022-12-16 add MotorShaftFlattening variable
    [6.stl, parametric-3d-rotator.scad]
2022-12-17 gear size, #0 and #10, bugfix|render
    [0.stl, 1.stl, 10.stl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]
2022-12-18 add new parameters, update #1, #7 and #13, bugfix|render
    [0.stl, 1.stl, 10.stl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]
2022-12-23 add some variables, modify readme
    [parametric-3d-rotator.scad]
2022-12-23 redesign S size, add .3mf, modify readme
    [0.stl, 1.stl, 10.stl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]
2022-12-23 add XL.3mf, modify readme
    [XL_in.3mf, XL_out1.3mf, XL_out2.3mf]
2022-12-24 add new motor terminal and modify
    [0.stl, 1.stl, 10.stl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]
2022-12-24 update 3mf | render
    [M_in.3mf, M_out.3mf, XL_in.3mf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]
2022-12-26 redesign #7, #8, add output terminal.DXF|render
    [0.stl, 1.stl, 10.stl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]
2022-12-26 V cut in gear for assembly
    [parametric-3d-rotator.scad]
2022-12-26 expand eye for wire
    [parametric-3d-rotator.scad]
2022-12-27 modify part #8
    [parametric-3d-rotator.scad]
2022-12-27 fix part #0
    [parametric-3d-rotator.scad]
2022-12-29 add 3 Vcut to part #3, fix height #9 | render
    [0.stl, 1.stl, 10.stl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]
2022-12-30 fix #8 | render
    [8.stl, M_in.3mf, XL_in.3mf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]
2023-01-22 M measure, modify readme
    [M_in.3mf, M_out.3mf, parametric-3d-rotator.scad]
2023-01-22 #10 screw head size fix|#0 resize hole for M4 screw driver|readme
    [parametric-3d-rotator.scad]
2023-01-28 12 redesign|07 add binder|08 custom terminal+M4 screw|10 screw dia fix
    [parametric-3d-rotator.scad]
2023-06-12 add MS size|small changes|complete export
    [0.stl, 1.stl, 10.stl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]
